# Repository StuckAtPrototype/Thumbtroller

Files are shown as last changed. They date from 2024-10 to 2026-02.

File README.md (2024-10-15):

# Thumbtroller - StuckAtPrototype

Remote for the racer car project

https://github.com/StuckAtPrototype/Racer

## Youtube Video
A bit of a back-story of how this project came to be.

My Kickstarter failed, so I open sourced it (https://www.youtube.com/watch?v=6jzG-BMannc)

Sub if you like what you see.

## Project Structure
The project consists of
1. Firmware
2. Hardware
3. Mechanical 

#### Requirements
- ESP32 IDF version 5.3.1
- USB to Serial dongle
- Target set to ESP32-H2

---
## License
### Apache 2.0 -- i.e. use as you'd like
http://www.apache.org/licenses/LICENSE-2.0

--- 
## Special Thanks
Thanks to Michael Angerer for his open sourced `esp32_ble_ota` project. I used it to get BLE running in this project. His blog post and github repo are a great resource. Check it out. https://github.com/michael-angerer/esp32_ble_ota

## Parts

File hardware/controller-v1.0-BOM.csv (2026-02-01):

Designator | Quantity | Manufacturer Part Number | Package/Footprint | Description
C5 | 1 | GRM188R60J226MEA0J | C_0603_1608Metric | 22uF
C16,C20,C18,C17,C19,C14 | 6 | CC0603KRX5R8BB105 | C_0603_1608Metric | 1uF
R25,R22,R23,R26,R24 | 5 | WR06X1003FTL | R_0603_1608Metric | 100K
C1,C3,C2,C4,C7 | 5 | GRM188R61A106ME69D | C_0603_1608Metric | 10uF
R1 | 1 | RQ73C1J806RBTDF | R_0603_1608Metric | 806
C12,C9,C13,C15,C11,C10 | 6 | CC0603KRX7R7BB104 | C_0603_1608Metric | 0.1uF
R9 | 1 | RMCF0603FT1M00 | R_0603_1608Metric | 1M
R14,R13,R18,R6,R19,R17,R16,R12,R27,R20,R21 | 11 | WR06X103 JTL | R_0603_1608Metric | 10K
C8 | 1 | GRM188C80E476ME05D | C_0603_1608Metric | 47uF
Q1 | 1 | BSS138 | SOT-23 | BSS138
R5,R8,R7 | 3 | RC0603FR-075K1L | R_0603_1608Metric | 5K1
U3 | 1 | MCP73833T-AMI/MF | SON50P300X300X100-11N | MCP73833
D3 | 1 | 150060RS75000 | C_0603_1608Metric | LED_RED
S1 | 1 | JS102011SAQN | SW_JS102011SAQN | JS102011SAQN
R15 | 1 | ESR03EZPF4700 | R_0603_1608Metric | 470
D2 | 1 | 150060GS75000 | C_0603_1608Metric | LED_GREEN
R2 | 1 | RT0603BRE071K43L | R_0603_1608Metric | 1.43K
U1 | 1 | AP2205-33W5-7 | AP2204 | AP2205
R11,R10 | 2 | RC0603JR-07330RL | R_0603_1608Metric | 330
J1 | 1 | S2B-PH-SM4-TB | JST_PH_S2B-PH-SM4-TB_1x02-1MP_P2.00mm_Horizontal | JST 2.0 BATT
TH1 | 1 | NTCG163JF103HT1 | R_0603_1608Metric | TH 10K
R3 | 1 | CR0603-FX-91R0ELF | R_0603_1608Metric | 91
L1 | 1 | CIGT252010EH1R0MNE | RES_CIGT252010 | 1uH
D1 | 1 | TPD1E10B06DYAR | D_SOD-523 | TPD1E10B06DPYR
U2 | 1 | TPS631000DRLR | TPS631000DRLR_TEX | TPS631000DRLR
C6 | 1 | CL10A225KO8NNNC | C_0603_1608Metric | 2.2uF
R4 | 1 | ERJ-PB3B7502V | R_0603_1608Metric | 75K
U4 | 1 | ESP32-H2-MINI-1-N4 | MODULE_ESP32-H2-MINI-1-H2 | ESP32-H2-MINI-1
P1 | 1 | USB4105-GF-A | GCT_USB4105-GF-A | USB_C_Plug_USB2.0
LED2,LED3,LED1 | 3 | IN-PI15TAT5R5G5B | IN-PI15_INL | IN-PI15TAT5R5G5B
S5,S3,S4,S2,S6 | 5 | PTS810 SJM 250 SMTR LFS | SW_PTS810_SJM_250_SMTR_LFS | TL4100AF240QG_
U5 | 1 | THB001P | CNK_THB001P | THB001P

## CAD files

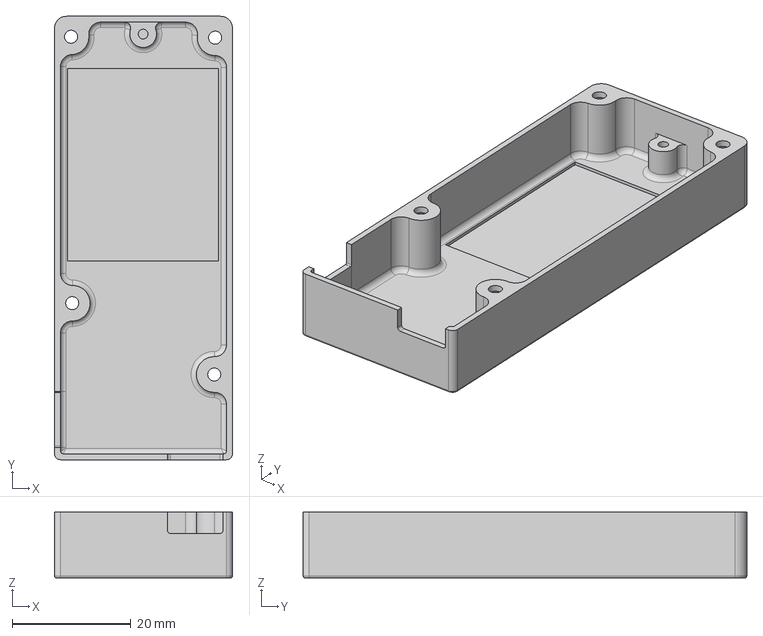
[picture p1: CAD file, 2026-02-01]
mechanical/Thumbtroller bottom cover v1.0.step
30.0 x 74.7 x 11.1 mm

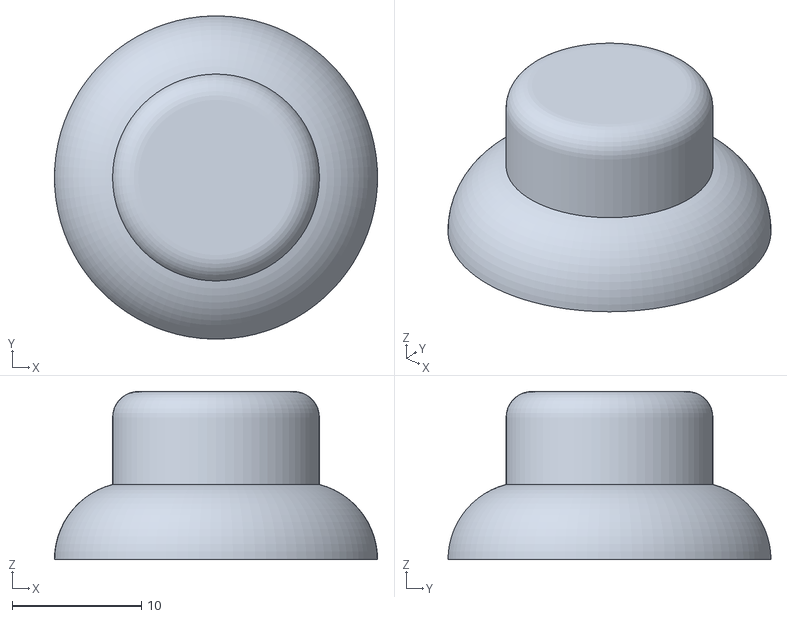
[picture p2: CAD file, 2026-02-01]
mechanical/Thumbtroller thumbstick v1.0.stl
25.0 x 25.0 x 13.0

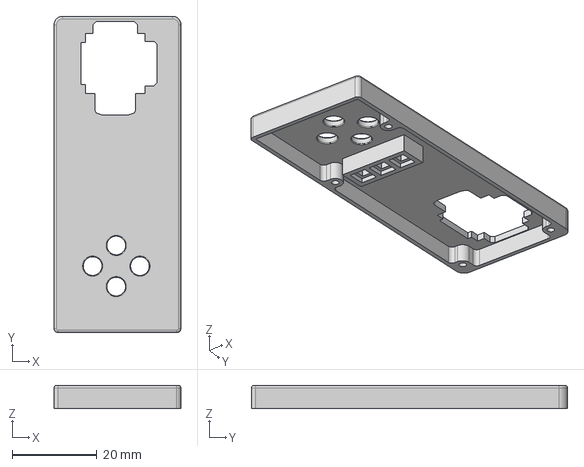
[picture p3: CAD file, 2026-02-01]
mechanical/Thumbtroller top cover v1.0.step
30.0 x 74.7 x 5.50 mm

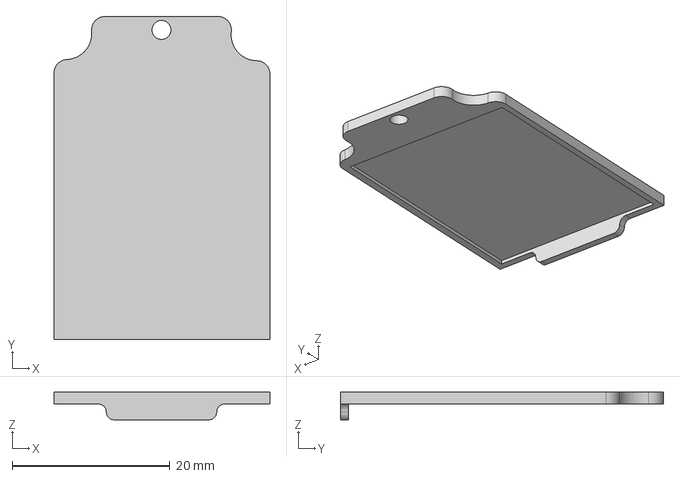
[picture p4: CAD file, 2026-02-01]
mechanical/Thumbtroller battery cover v1.0.step
27.4 x 40.9 x 3.50 mm

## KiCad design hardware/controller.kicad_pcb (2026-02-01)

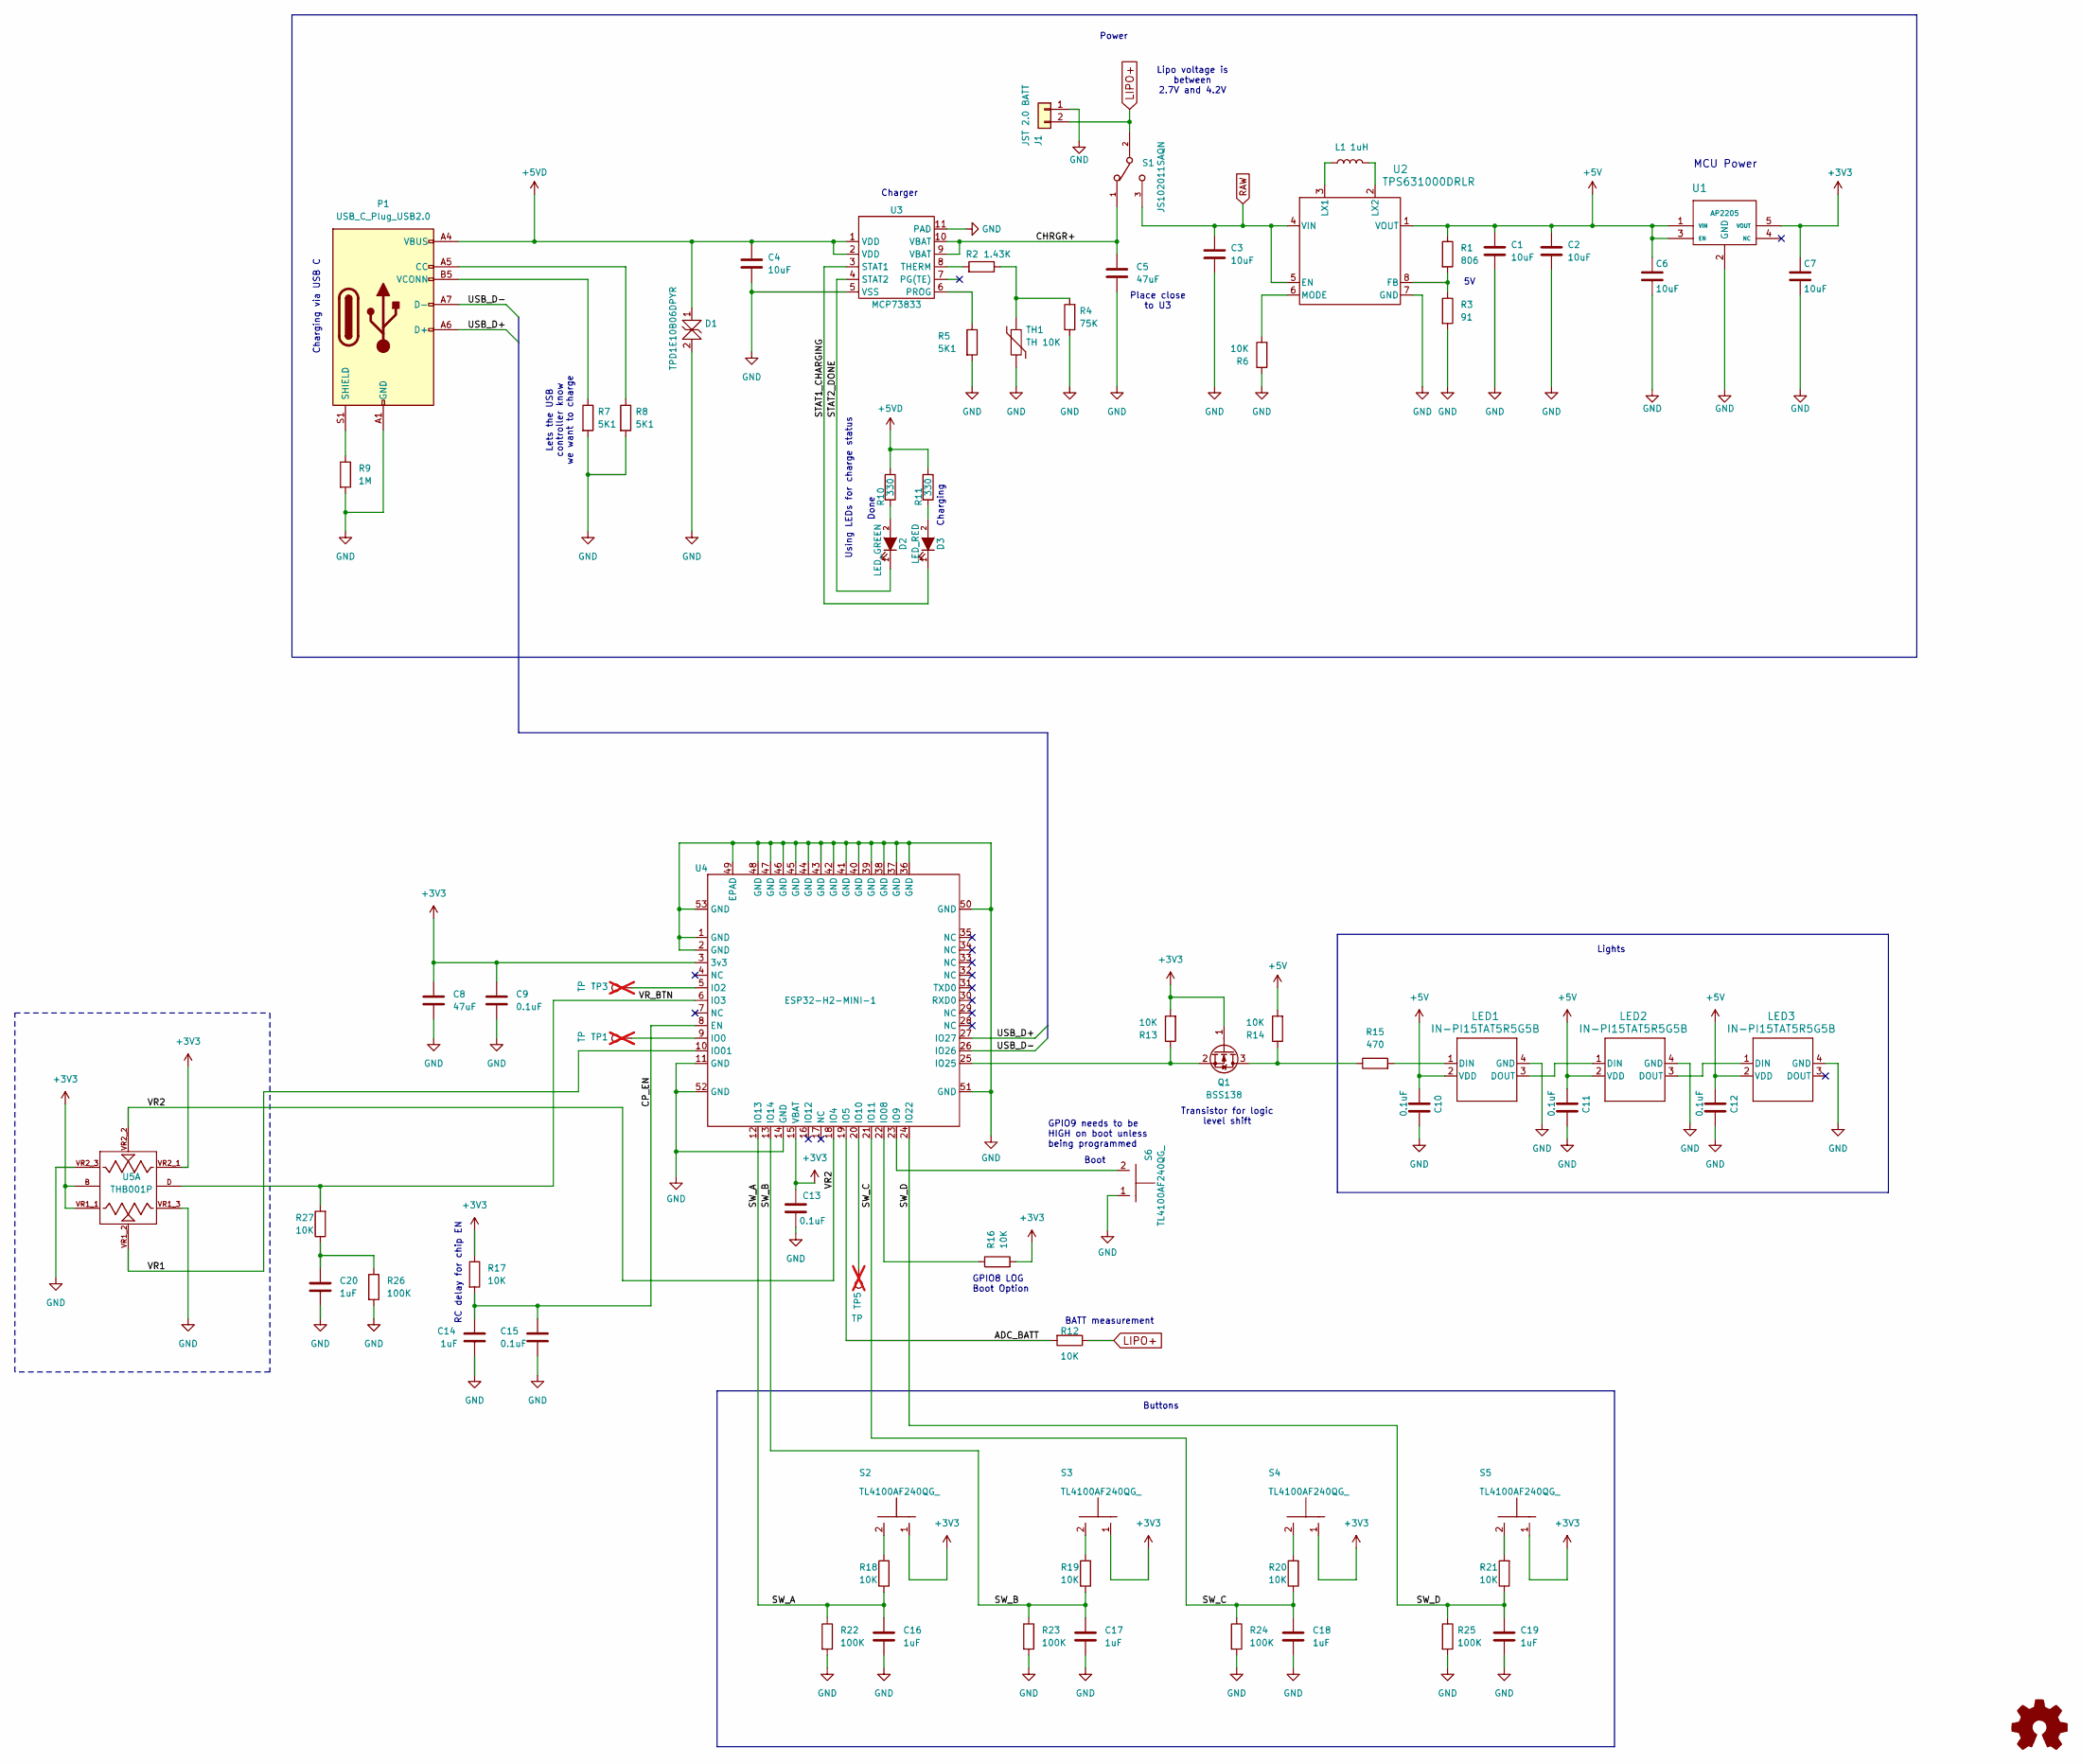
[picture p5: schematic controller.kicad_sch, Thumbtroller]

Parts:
C1, C2, C3, C4, C6, C7: 10uF; C_0603_1608Metric
C5, C8: 47uF; C_0603_1608Metric
C9, C10, C11, C12, C13, C15: 0.1uF; C_0603_1608Metric
C14, C16, C17, C18, C19, C20: 1uF; C_0603_1608Metric
D1: TPD1E10B06DPYR; D_SOD-523
D2: LED_GREEN; C_0603_1608Metric
D3: LED_RED; C_0603_1608Metric
J1: JST 2.0 BATT; JST_PH_S2B-PH-SM4-TB_1x02-1MP_P2.00mm_Horizontal
L1: 1uH; RES_CIGT252010
LED1, LED2, LED3: IN-PI15TAT5R5G5B; IN-PI15_INL
P1: USB_C_Plug_USB2.0; GCT_USB4105-GF-A
Q1: BSS138; SOT-23
R1: 806; R_0603_1608Metric
R2: 1.43K; R_0603_1608Metric
R3: 91; R_0603_1608Metric
R4: 75K; R_0603_1608Metric
R5, R7, R8: 5K1; R_0603_1608Metric
R6, R12, R13, R14, R16, R17, R18, R19, R20, R21, R27: 10K; R_0603_1608Metric
R9: 1M; R_0603_1608Metric
R10, R11: 330; R_0603_1608Metric
R15: 470; R_0603_1608Metric
R22, R23, R24, R25, R26: 100K; R_0603_1608Metric
S1: JS102011SAQN; SW_JS102011SAQN
S2, S3, S4, S5, S6: TL4100AF240QG_; SW_PTS810_SJM_250_SMTR_LFS
TH1: TH 10K; R_0603_1608Metric
TP1, TP3, TP5: TP; TestPoint_Pad_1.5x1.5mm; not fitted
U1: AP2205; AP2204
U2: TPS631000DRLR; TPS631000DRLR_TEX
U3: MCP73833; SON50P300X300X100-11N
U4: ESP32-H2-MINI-1; MODULE_ESP32-H2-MINI-1-H2
U5: THB001P; CNK_THB001P; PARTREV 27 Jan 22

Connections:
+3V3: C7.1, C8.1, C9.1, C13.1, Q1.1 (G), R13.2, R16.2, R17.1, S2.1, S3.1, S4.1, S5.1, U1.5 (VOUT), U4.3 (3v3), U4.15 (VBAT), U5.B, U5.VR1_1, U5.VR2_1
+5V: C1.1, C2.1, C6.1, C10.1, C11.1, C12.1, LED1.2 (VDD), LED2.2 (VDD), LED3.2 (VDD), R1.1, R14.2, U1.1 (VIN), U1.3 (EN), U2.1 (VOUT)
+5VD: C4.1, D1.1, P1.A4 (VBUS), P1.A9 (VBUS), P1.B4 (VBUS), P1.B9 (VBUS), R10.1, R11.1, U3.1 (VDD), U3.2 (VDD)
/ADC_BATT: R12.2, U4.19 (IO5)
/CHRGR+: C5.1, S1.1, U3.9 (VBAT), U3.10 (VBAT)
/CP_EN: C14.1, C15.1, R17.2, U4.8 (EN)
/STAT1_CHARGING: D3.1 (K), U3.3 (STAT1)
/STAT2_DONE: D2.1 (K), U3.4 (STAT2)
/SW_A: C16.1, R18.1, R22.1, U4.12 (IO13)
/SW_B: C17.1, R19.1, R23.1, U4.13 (IO14)
/SW_C: C18.1, R20.1, R24.1, U4.21 (IO11)
/SW_D: C19.1, R21.1, R25.1, U4.24 (IO22)
/USB_D+: P1.A6 (D+), U4.27 (IO27)
/USB_D-: P1.A7 (D-), U4.26 (IO26)
/VR1: U4.10 (IO01), U5.VR1_2
/VR2: U4.18 (IO4), U5.VR2_2
/VR_BTN: R27.2, U4.6 (IO3), U5.D
GND: C1.2, C2.2, C3.2, C4.2, C5.2, C6.2, C7.2, C8.2, C9.2, C10.2, C11.2, C12.2, C13.2, C14.2, C15.2, C16.2, C17.2, C18.2, C19.2, C20.2, D1.2, J1.1, LED1.4 (GND), LED2.4 (GND), LED3.4 (GND), P1.A1 (GND), P1.A12 (GND), P1.B1 (GND), P1.B12 (GND), R3.2, R4.1, R5.2, R6.1, R7.2, R8.2, R9.2, R22.2, R23.2, R24.2, R25.2, R26.2, S6.1, TH1.2, U1.2 (GND), U2.7 (GND), U3.5 (VSS), U3.11 (PAD), U4.1 (GND), U4.2 (GND), U4.11 (GND), U4.14 (GND), U4.36 (GND), U4.37 (GND), U4.38 (GND), U4.39 (GND), U4.40 (GND), U4.41 (GND), U4.42 (GND), U4.43 (GND), U4.44 (GND), U4.45 (GND), U4.46 (GND), U4.47 (GND), U4.48 (GND), U4.49 (EPAD), U4.50 (GND), U4.51 (GND), U4.52 (GND), U4.53 (GND), U5.VR1_3, U5.VR2_3
LIPO+: J1.2, R12.1, S1.2
unnamed: C20.1, R26.1, R27.1
unnamed: D2.2 (A), R10.2
unnamed: D3.2 (A), R11.2
unnamed: LED1.1 (DIN), R15.2
unnamed: LED1.3 (DOUT), LED2.1 (DIN)
unnamed: LED2.3 (DOUT), LED3.1 (DIN)
unnamed: P1.A5 (CC), R8.1
unnamed: P1.S1 (SHIELD), R9.1
unnamed: P1.B5 (VCONN), R7.1
unnamed: Q1.3 (D), R14.1, R15.1
unnamed: Q1.2 (S), R13.1, U4.25 (IO25)
unnamed: R2.1, R4.2, TH1.1
unnamed: R18.2, S2.2
unnamed: R19.2, S3.2
unnamed: R20.2, S4.2
unnamed: R21.2, S5.2
unnamed: R1.2, R3.1, U2.8 (FB)
unnamed: L1.1, U2.3 (LX1)
unnamed: L1.2, U2.2 (LX2)
unnamed: R6.2, U2.6 (MODE)
unnamed: R5.1, U3.6 (PROG)
unnamed: R2.2, U3.8 (THERM)
unnamed: TP1.1, U4.9 (IO0)
unnamed: TP3.1, U4.5 (IO2)
unnamed: R16.1, U4.22 (IO08)
unnamed: S6.2, U4.23 (IO9)
unnamed: TP5.1, U4.20 (IO10)
RAW: C3.1, S1.3, U2.4 (VIN), U2.5 (EN)

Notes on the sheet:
Lights
Place close to U3
MCU Power
RC delay for chip EN
Transistor for logic level shift
Charging via USB C
BATT measurement
GPIO8 LOG Boot Option
Boot
GPIO9 needs to be HIGH on boot unless being programmed
Power
Lipo voltage is between 2.7V and 4.2V
Using LEDs for charge status
Charger
Done
Charging
Buttons
Lets the USB controller know we want to charge

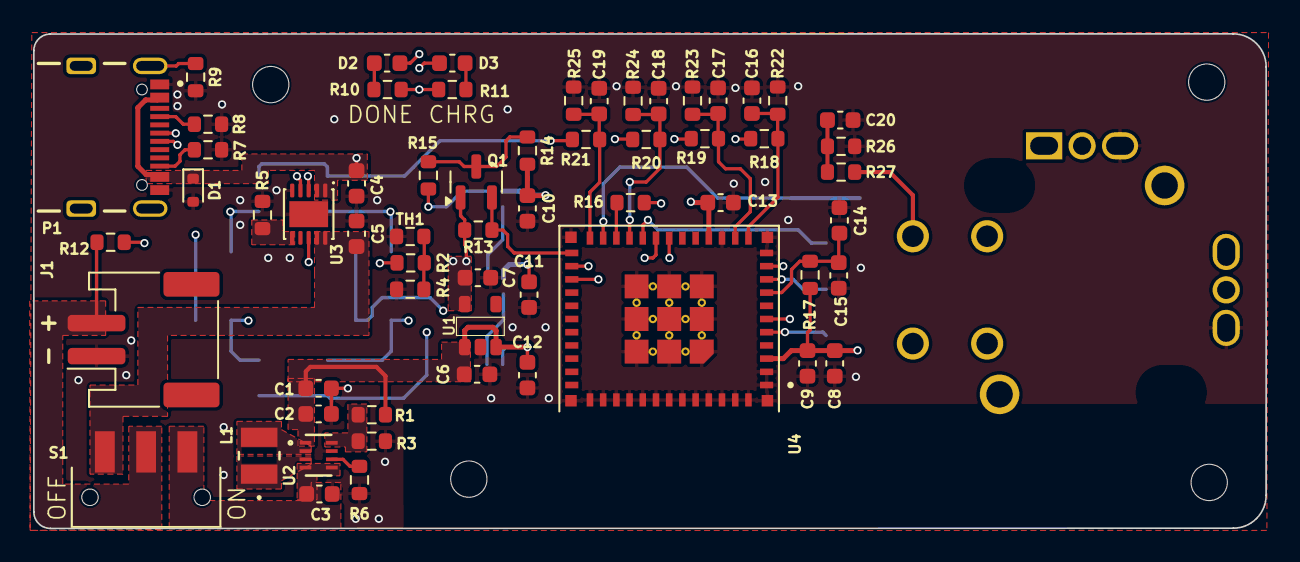
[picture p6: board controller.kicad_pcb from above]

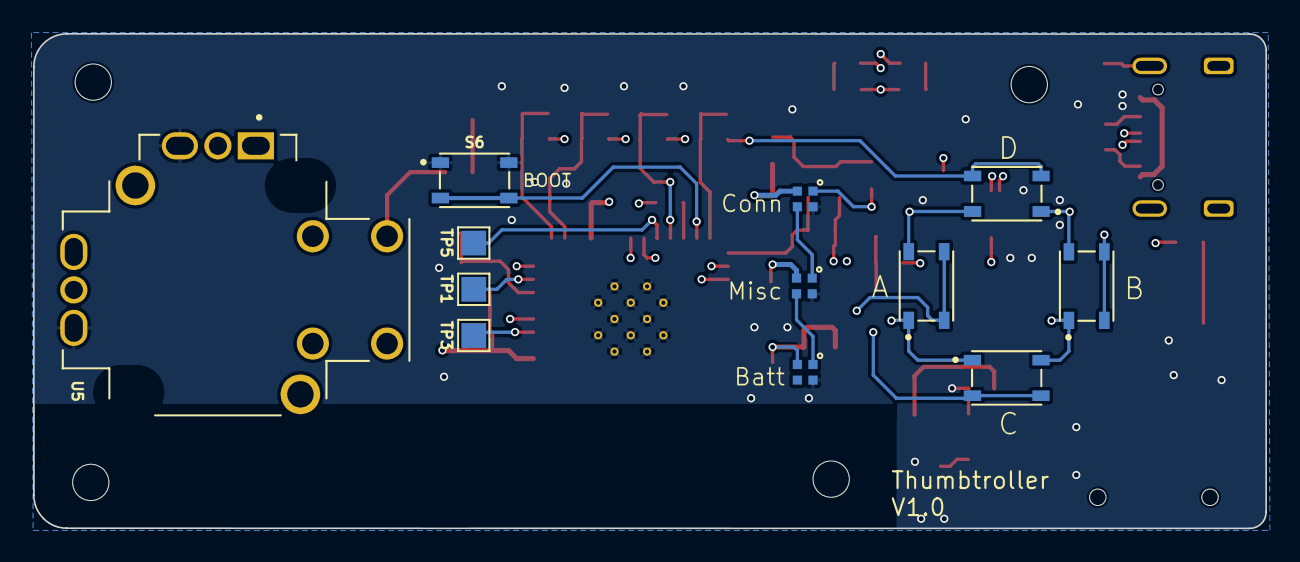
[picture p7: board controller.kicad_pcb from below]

Board: 4 copper layers, 74.7 x 30.0 mm, 72 parts (12 on the bottom side), 47 nets.

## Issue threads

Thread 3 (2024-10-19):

KiCad PCB is a four layer board with empty inner layers.

majorChange, 2024-10-19:
In KiCad the board is definded a four layer board but the inner layers are empty. The design seems to be two layers only. that could be a problem for anyone ordering this board.

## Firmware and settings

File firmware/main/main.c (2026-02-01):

#include <stdio.h>
#include <inttypes.h>
#include "sdkconfig.h"
#include "freertos/FreeRTOS.h"
#include "freertos/task.h"
#include "freertos/queue.h"
#include "freertos/semphr.h"
#include "esp_chip_info.h"
#include "esp_flash.h"
#include "esp_system.h"
#include "esp_log.h"
#include "driver/gpio.h"

// BLE
#include "gap.h"
#include "gatt_svr.h"
#include "nvs_flash.h"
#include "esp_bt.h"

#include "led.h"
#include "led_color_lib.h"
#include "ws2812_control.h"

// adc
#include "adc_reader.h"

// button interrupt
#include "button_isr.h"

// game logic
#include "game_logic.h"

struct led_state new_state1;

void app_main(void)
{
    // initialize the leds
    led_init();

    // set the initial sate of the LEDs
    led_batt_set(0);
    led_conn_set(0);
    led_status_color_set(LED_COLOR_BLUE);

    gpio_num_t button_pins[] = {GPIO_NUM_13, GPIO_NUM_14, GPIO_NUM_11, GPIO_NUM_22, GPIO_NUM_3};
    QueueHandle_t button_events = xQueueCreate(10, sizeof(gpio_num_t));

    button_isr_init(button_pins, 5, button_events);

    xTaskCreate(button_isr_debounce_task, "btn_debounce", 2048,
                NULL, 10, NULL);

    // BLE Setup -------------------
    nimble_port_init();
    ble_hs_cfg.sync_cb = sync_cb;
    ble_hs_cfg.reset_cb = reset_cb;
    gatt_svr_init();
    ble_svc_gap_device_name_set(device_name);
    nimble_port_freertos_init(host_task);

    // Initialize ADC
    esp_err_t result = adc_init();
    if (result != ESP_OK) {
        printf("ADC initialization failed\n");
        return;
    }

    game_init();

    // all the main logic is happening within game logic loop
    xTaskCreate(game_logic_loop, "game_logic_loop", 4096, NULL, 1, NULL);

    while (1) {


        vTaskDelay(200 / portTICK_PERIOD_MS);  // Delay for 200 ms
    }
}

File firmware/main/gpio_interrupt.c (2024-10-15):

#include "gpio_interrupt.h"
#include <stdio.h>
#include "freertos/task.h"
#include "driver/gpio.h"

#define GPIO_QUEUE_LENGTH 10
#define GPIO_QUEUE_ITEM_SIZE sizeof(uint32_t)
#define DEBOUNCE_TIME_MS 200

QueueHandle_t gpio_evt_queue = NULL;

static void IRAM_ATTR gpio_isr_handler(void* arg)
{
    static uint32_t last_interrupt_time = 0;
    uint32_t interrupt_time = xTaskGetTickCountFromISR();
    uint32_t gpio_num = (uint32_t) arg;

    // Check if it's a falling edge
    if (gpio_get_level(gpio_num) == 1) {
        // Debounce mechanism
        if (interrupt_time - last_interrupt_time > pdMS_TO_TICKS(DEBOUNCE_TIME_MS)) {
            xQueueSendFromISR(gpio_evt_queue, &gpio_num, NULL);
            last_interrupt_time = interrupt_time;
        }
    }
}

void configure_gpio_interrupt(void)
{
    // Create a queue to handle GPIO event from ISR
    gpio_evt_queue = xQueueCreate(GPIO_QUEUE_LENGTH, GPIO_QUEUE_ITEM_SIZE);

    // Configure the GPIO pin
    gpio_config_t io_conf = {};
    io_conf.intr_type = GPIO_INTR_POSEDGE;  // Interrupt on falling edge only
    io_conf.pin_bit_mask = (1ULL << INTERRUPT_PIN_A) | (1ULL << INTERRUPT_PIN_B);  // Bit mask of the pin
    io_conf.mode = GPIO_MODE_INPUT;  // Set as input
    io_conf.pull_up_en = GPIO_PULLUP_DISABLE;  // Enable pull-up resistor
    io_conf.pull_down_en = GPIO_PULLDOWN_DISABLE;  // Disable pull-down resistor
    gpio_config(&io_conf);

    // Install GPIO ISR service
    gpio_install_isr_service(0);

    // Attach the interrupt service routine
    gpio_isr_handler_add(INTERRUPT_PIN_A, gpio_isr_handler, (void*) INTERRUPT_PIN_A);
    gpio_isr_handler_add(INTERRUPT_PIN_B, gpio_isr_handler, (void*) INTERRUPT_PIN_B);

}

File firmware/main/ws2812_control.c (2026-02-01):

#include "ws2812_control.h"
#include "driver/rmt_tx.h"
#include "esp_err.h"
#include "esp_check.h"
#include "freertos/FreeRTOS.h"
#include "esp_log.h"

#define LED_RMT_TX_GPIO         25
#define BITS_PER_LED_CMD        24
#define LED_BUFFER_ITEMS        (NUM_LEDS * BITS_PER_LED_CMD)

// Assuming 10MHz resolution
#define T0H     3  // 0 bit high time
#define T1H     6  // 1 bit high time
#define T0L     8  // 0 bit low time
#define T1L     5  // 1 bit low time

static const char *TAG = "NeoPixel WS2812 Driver";

static rmt_channel_handle_t led_chan = NULL;
static rmt_encoder_handle_t led_encoder = NULL;
static uint8_t led_data_buffer[NUM_LEDS * 3]; // 3 bytes per LED (RGB)

static size_t ws2812_rmt_encode(rmt_encoder_t *encoder, rmt_channel_handle_t channel, const void *primary_data, size_t data_size, rmt_encode_state_t *ret_state)
{
    rmt_encoder_handle_t bytes_encoder = (rmt_encoder_handle_t)encoder;
    rmt_encode_state_t session_state = 0;
    size_t encoded_symbols = bytes_encoder->encode(bytes_encoder, channel, primary_data, data_size, &session_state);
    *ret_state = session_state;
    return encoded_symbols;
}

esp_err_t ws2812_control_init(void)
{
    ESP_LOGI(TAG, "Create RMT TX channel");
    rmt_tx_channel_config_t tx_chan_config = {
            .gpio_num = LED_RMT_TX_GPIO,
            .clk_src = RMT_CLK_SRC_DEFAULT,
            .resolution_hz = 10 * 1000 * 1000, // 10MHz resolution
            .mem_block_symbols = 64,
            .trans_queue_depth = 4,
    };
    ESP_RETURN_ON_ERROR(rmt_new_tx_channel(&tx_chan_config, &led_chan), TAG, "Failed to create RMT TX channel");

    ESP_LOGI(TAG, "Install led strip encoder");
    rmt_bytes_encoder_config_t bytes_encoder_config = {
            .bit0 = {
                    .level0 = 1,
                    .duration0 = T0H,
                    .level1 = 0,
                    .duration1 = T0L,
            },
            .bit1 = {
                    .level0 = 1,
                    .duration0 = T1H,
                    .level1 = 0,
                    .duration1 = T1L,
            },
            .flags.msb_first = 1,
    };
    ESP_RETURN_ON_ERROR(rmt_new_bytes_encoder(&bytes_encoder_config, &led_encoder), TAG, "Failed to create bytes encoder");

    ESP_LOGI(TAG, "Enable RMT TX channel");
    ESP_RETURN_ON_ERROR(rmt_enable(led_chan), TAG, "Failed to enable RMT channel");

    return ESP_OK;
}

esp_err_t ws2812_write_leds(struct led_state new_state)
{
    for (uint32_t led = 0; led < NUM_LEDS; led++) {
        uint32_t bits_to_send = new_state.leds[led];
        led_data_buffer[led * 3 + 0] = (bits_to_send >> 16) & 0xFF; // Red
        led_data_buffer[led * 3 + 1] = (bits_to_send >> 8) & 0xFF;  // Green
        led_data_buffer[led * 3 + 2] = bits_to_send & 0xFF;         // Blue
    }

    rmt_transmit_config_t tx_config = {
            .loop_count = 0,
    };

    ESP_RETURN_ON_ERROR(rmt_transmit(led_chan, led_encoder, led_data_buffer, sizeof(led_data_buffer), &tx_config), TAG, "Failed to transmit RMT data");
    ESP_RETURN_ON_ERROR(rmt_tx_wait_all_done(led_chan, portMAX_DELAY), TAG, "Failed to wait for RMT transmission to finish");

    return ESP_OK;
}

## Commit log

2024-10-15 version 0.2
    [enclosure-cover.step, main-enclosure.step]
2024-10-19 adding hardware files and BOM for the remote
    [controller-v0.2-BOM.csv, controller.kicad_pcb, controller.kicad_sch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]
2025-10-25 3D files v1.0
    [Thumbtroller battery cover v1.0.step, Thumbtroller bottom cover v1.0.step, Thumbtroller thumbstick v1.0.stl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]
2025-10-25 hardware v1.0
    [controller-v0.2-BOM.csv, controller-v1.0-BOM.csv, controller.kicad_pcb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]
